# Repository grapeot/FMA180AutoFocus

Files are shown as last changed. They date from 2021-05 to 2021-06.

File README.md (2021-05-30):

## 锐星FMA180自动对焦解决方案

[[English version]](#english)

最近买了一个锐星的FMA180打算拍广域。这个镜子因为口径特别小（40mm f/4.5，焦距180mm），所以没有配一般的对焦器，而是像镜头一样在镜身上有个对焦环。因为用的ZWO EAF默认只支持望远镜对焦器，所以买了传动皮带做了一个自动对焦的装置。分享一下。

其实思路非常简单，就是3D打印一个鸠尾板，然后打印一个装置把EAF用螺丝固定在鸠尾板上。然后用皮带把望远镜（或者其他镜头）的对焦环和EAF连接起来即可。设计出来的模型可以在github下载：https://github.com/grapeot/FMA180AutoFocus/ 。模型如下图：

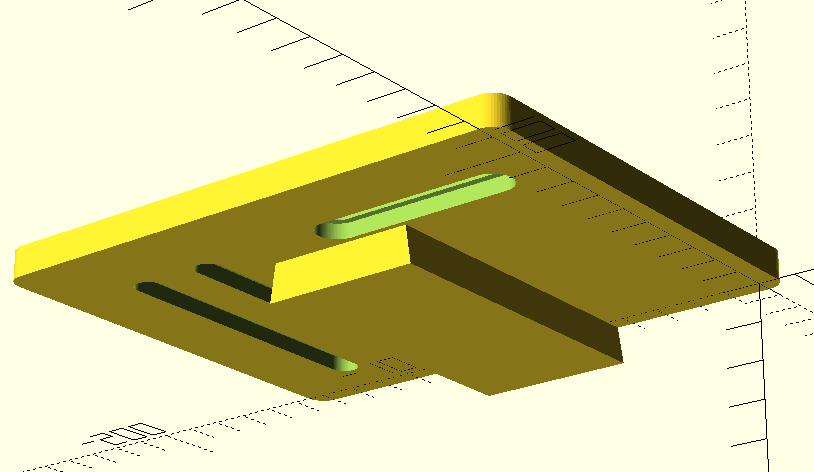
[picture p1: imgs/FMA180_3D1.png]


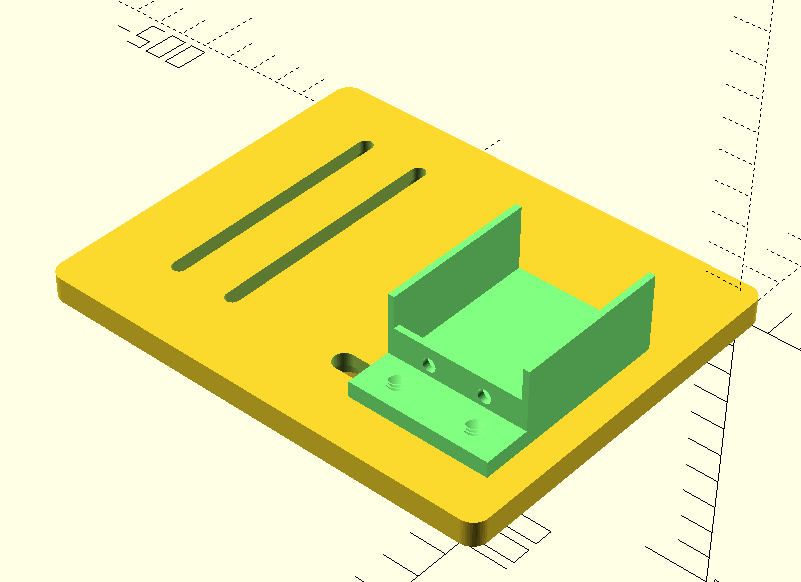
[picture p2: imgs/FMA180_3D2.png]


有几个需要注意的地方：

1. 皮带用的就是GT2皮带，3D打印机上很多也是这种。配套的滑轮（不确定是不是应该叫滑轮？pulley）是5mm的。皮带长度我用的是280mm，这样配套FMA180和鸠尾板的长度正好适配。如果用了其他镜头或者皮带需要重新调整参数。
2. 因为对焦环是凸出来的，所以如果直接安装的话会卡死鸠尾板，导致皮带装不进去。所以我们还需要在上面放四个垫圈。垫圈也是可以打印的，见washer.stl。另外两个STL文件一个是鸠尾板一个是EAF支架。我用的是OpenSCAD开发的，源文件也放进去了。
3. 装配非常简单。基本上把螺丝拧上就好了。固定望远镜用的是随镜附赠的M4螺丝，注意拧的时候要套上垫圈。固定EAF用的是EAF带的M4螺丝（螺距和FMA的M4还不一样）。把EAF支架固定在鸠尾板上用的是M6螺丝，需要另外购买。建议的装配顺序是，先装EAF支架，不要拧死螺丝。然后装FMA主镜，也不要拧死螺丝。然后安装皮带，调整FMA和EAF的位置，左右调EAF，前后调FMA，使得对焦环和EAF平齐，皮带有一定张力。拧紧螺丝。注意EAF支架的螺丝不要太紧，否则可能会破坏打印出来的螺纹。
4. 这个对焦环有个坑是对焦的时候自己会前后跑。所以我的设计是有缺陷的。好在EAF自动对焦的行程不长，只要事先大致拧到合焦的位置（刻度大约是10附近），然后调整FMA的前后位置即可。实测这样是可以可靠自动对焦的。

最终的成品类似这样：

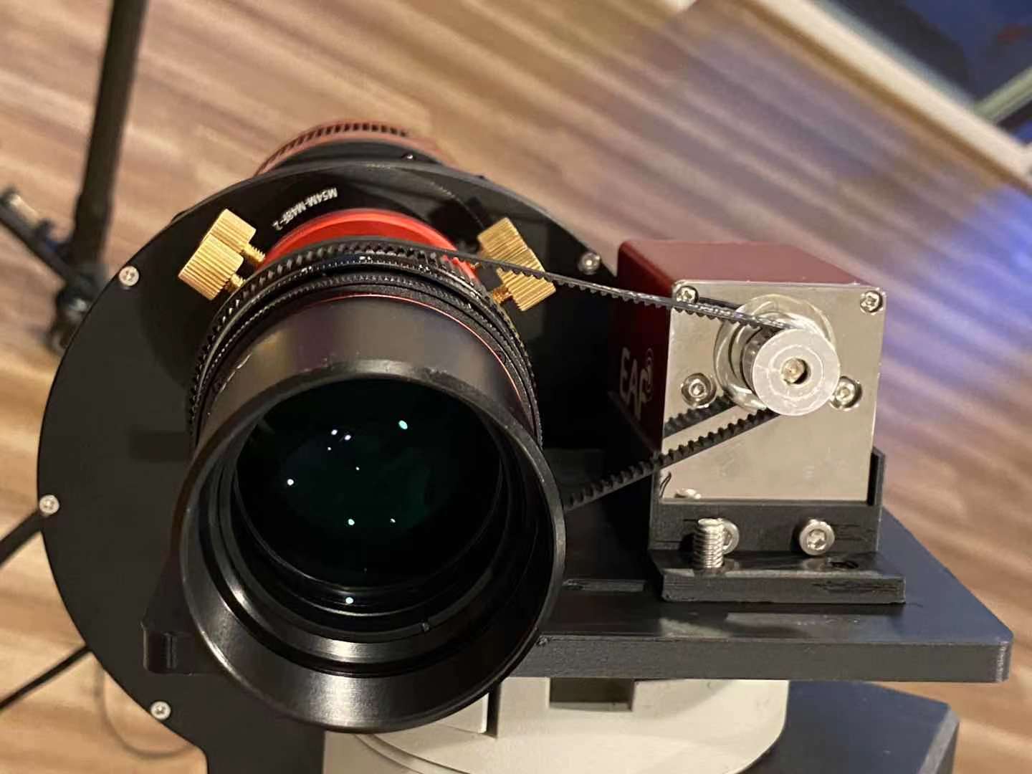
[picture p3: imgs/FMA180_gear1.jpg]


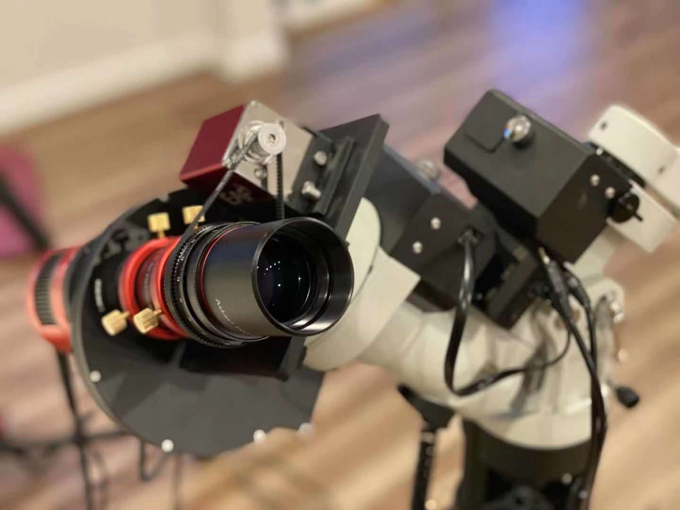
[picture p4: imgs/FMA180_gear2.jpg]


开光拍了个Ha通道2x4的马赛克，总共3小时曝光，效果如图：

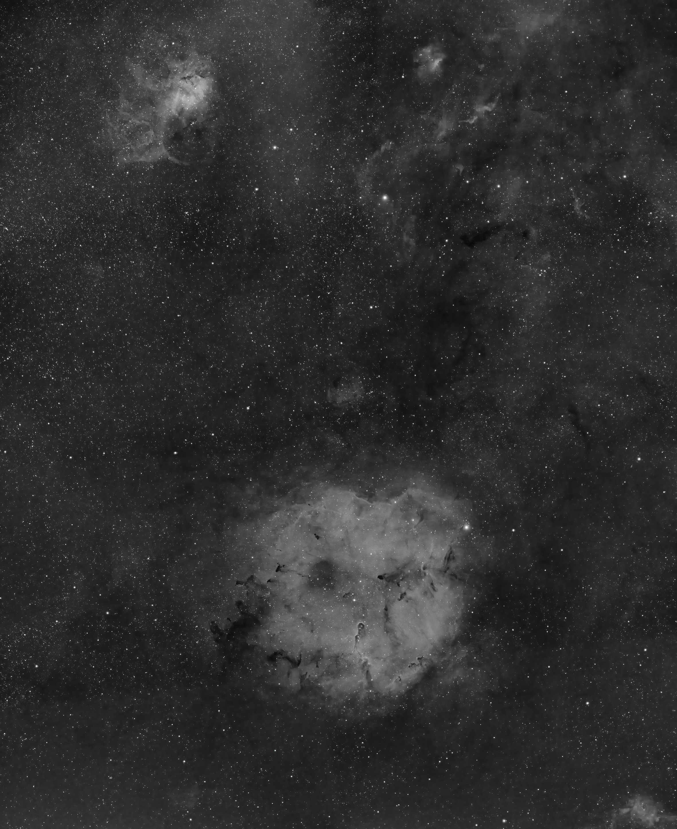
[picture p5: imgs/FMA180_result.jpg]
Result image


## Auto focus solution for SharpStar FMA180

Bought a SharpStar FMA180 recently for wide field use.
Probably because of the small aperture (40mm f/4.5, 180mm focal length), it doesn't come with a regular focuser, but has a focus ring just like regular lens.
But the ZWO EAF I use only supports telescope-style focusers.
So I use a belt to make the EAF work with the FMA180.

The idea is simple.
Just print a dovetail to hold both the scope and a EAF rack, which is then fixed to the dovetail using screws.
The focus ring of the scope (or any lens) can be connected to the EAF via a belt.
The 3d models and instructions can be downloaded on github: https://github.com/grapeot/FMA180AutoFocus/ .
The rendered models look like this:

Rendered model

Rendered model

Several points worth noting:

1. The belt is regular GT2 belt, which can often be found on 3D printers. The The pulley has a bore of 5mm. I use a 280mm length belt, so it fits the FMA180 and the dovetail. When using a belt with a different length or a different scope, you need to adjust the parameters of the dovetail model.
2. Because the focus ring is a bit taller than the scope body, the belt cannot be installed if we directly screw the scope to the dovetail. In this case, four washers are needed between the dovetail and the scope. They are also printable -- check washer.stl. The other two STL files are for the dovetail and the EAF rack. I used OpenSCAD to develop, so I also put the .scad files in the repo.
3. Assembly is easy -- just using screws. To fix the scope to the dovetail, M4 screws with the scope are used. Don't forget to put the washers beforehand. To fix the EAF to the rack, the M4 screws coming with the EAF can be used. Interestingly these two M4 screws have different pitches. To fix the EAF rack to the dovetail, M6 screws are used. Note they need to be bought separately. The suggested assembly order is, first install the EAF rack but leave the screws loose. Then install the FMA scope. Leave the screws loose as well. Then install the belt. Adjust the positions of the FMA and the EAF, such that the EAF pulley and FMA focus ring are aligned, and the belt has enough tension. Then tighten the screws. Pay attention to the screws connecting the EAF rack and the dovetail. Don't over-tighten them. The threads are 3D printed on plastic anyway.
4. One caveat of FMA180 is the focus ring actually moves when focusing. My design doesn't accommodate this. So in order for the auto focus to work properly, before installing the FMA180, you need to roughly focus the scope. I find 10mm on the focus ring gives me good results. In this case, given the auto focus process has pretty limited movement, it can be performed reliably.

The final result looks like this:

Final result

Final result

And here is a result of 3 hours' Ha channel, from a 2x4 mosaic:

Result image

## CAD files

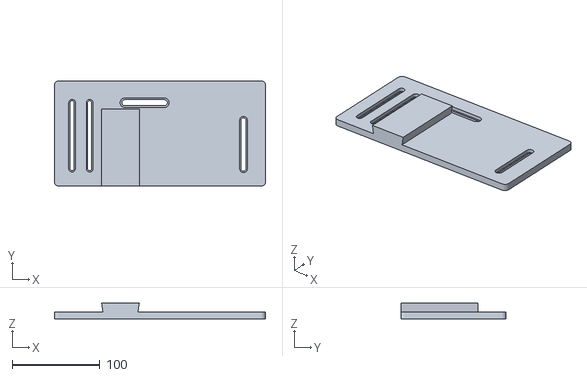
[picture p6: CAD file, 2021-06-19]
dovetail.stl
240.0 x 120.0 x 18.0

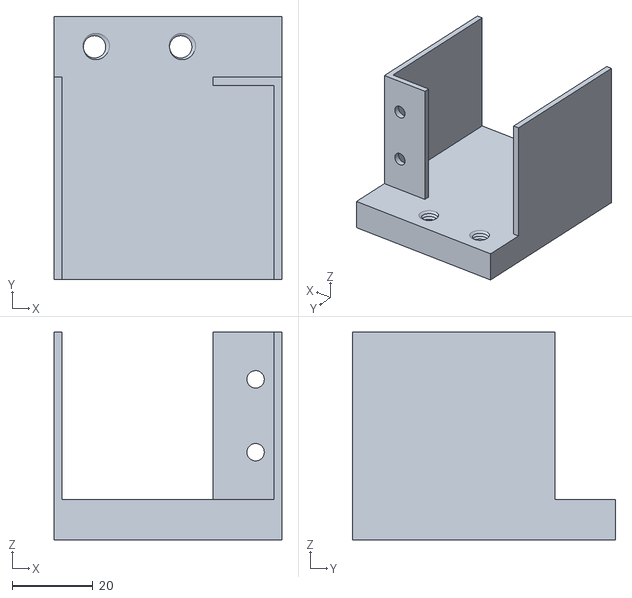
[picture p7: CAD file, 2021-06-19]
EAFRack.stl
56.3 x 65.0 x 51.3

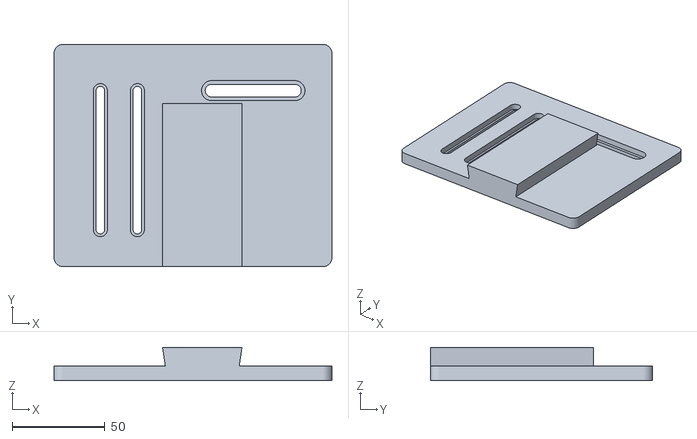
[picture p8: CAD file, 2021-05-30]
dovetail_no_guidescope.stl
150.0 x 120.0 x 18.0

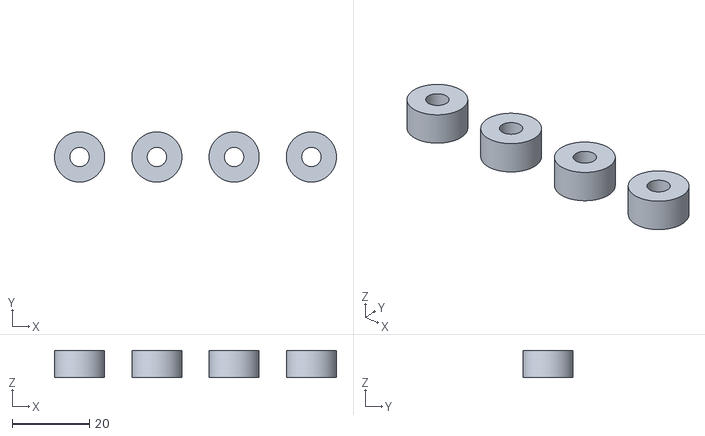
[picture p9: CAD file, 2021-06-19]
washer.stl
73.0 x 13.0 x 7.00

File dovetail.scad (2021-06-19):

include<EAFRack.scad>

module vixen_dovetail(len) {
    height = 10;
    body_height = 0;
    wall_depth = 10;
    margin = 0.6;
    width1 = 43.5 - margin;
    width2 = 40.5 - margin;

    translate([0, -height, 0])
    linear_extrude(height=len)
    polygon(points=[[-width1/2, 0], [-width1/2+wall_depth, 0],
      [-width2/2+wall_depth, height-wall_depth], [width2/2-wall_depth, height-wall_depth],
      [width1/2-wall_depth, 0], [width1/2, 0], 
      [width2/2, height], [-width2/2, height]]);
}

module dovetail_without_guidescope() {
    epsilon = 0.01;

    body_width = 150-10;
    body_height = 110;
    body_left = 15;
    body_top = 90;
    
    screw_upper_depth = 4;

    eaf_margin = 0.4;
    fma_margin = 0.3;

    difference() {
        // body
        linear_extrude(height=8)
        hull() {
            circle(r=5, $fn=50);
            translate([body_width, 0])
            circle(r=5, $fn=50);
            translate([0, body_height])
            circle(r=5, $fn=50);
            translate([body_width, body_height])
            circle(r=5, $fn=50);
        }

        // EAF holes
        // upper
        hull() {
            translate([body_left, body_top, 0])
            cylinder(r=3+eaf_margin, h=20, center=true, $fn=100);
            translate([body_left+45, body_top, 0])
            cylinder(r=3+eaf_margin, h=20, center=true, $fn=100);
        }
        // lower
        hull() {
            translate([body_left, body_top, -epsilon])
            cylinder(r=5+eaf_margin, h=screw_upper_depth, $fn=100);
            translate([body_left+45, body_top, -epsilon])
            cylinder(r=5+eaf_margin, h=screw_upper_depth, $fn=100);
        }

        // FMA holes
        // left
        // upper
        hull() {
            translate([body_left+85, body_top, 0])
            cylinder(r=2+fma_margin, h=20, center=true, $fn=100);
            translate([body_left+85, 15, 0])
            cylinder(r=2+fma_margin, h=20, center=true, $fn=100);
        }
        // lower
        hull() {
            translate([body_left+85, body_top, -epsilon])
            cylinder(r=3.5+fma_margin, h=screw_upper_depth, $fn=100);
            translate([body_left+85, 15, -epsilon])
            cylinder(r=3.5+fma_margin, h=screw_upper_depth, $fn=100);
        }
        // right
        // upper
        hull() {
            translate([body_left+105, body_top, 0])
            cylinder(r=2+fma_margin, h=20, center=true, $fn=100);
            translate([body_left+105, 15, 0])
            cylinder(r=2+fma_margin, h=20, center=true, $fn=100);
        }
        // lower
        hull() {
            translate([body_left+105, body_top, -epsilon])
            cylinder(r=3.5+fma_margin, h=screw_upper_depth, $fn=100);
            translate([body_left+105, 15, -epsilon])
            cylinder(r=3.5+fma_margin, h=screw_upper_depth, $fn=100);
        }
    }

    translate([body_width/2-5, body_height-27, 0])
    rotate([90, 0, 0])
    vixen_dovetail(body_height-22);
}

module dovetail() {
    epsilon = 0.01;

    body_width = 150-10+90;
    body_height = 110;
    body_left = 20;
    body_fma_left = body_left+90;
    body_top = 90;
    
    screw_upper_depth = 4;

    eaf_margin = 0.4;
    fma_margin = 0.3;

    difference() {
        // body
        linear_extrude(height=8)
        hull() {
            circle(r=5, $fn=50);
            translate([body_width, 0])
            circle(r=5, $fn=50);
            translate([0, body_height])
            circle(r=5, $fn=50);
            translate([body_width, body_height])
            circle(r=5, $fn=50);
        }

        // EAF holes
        // upper
        hull() {
            translate([body_fma_left, body_top, 0])
            cylinder(r=3+eaf_margin, h=20, center=true, $fn=100);
            translate([body_fma_left+45, body_top, 0])
            cylinder(r=3+eaf_margin, h=20, center=true, $fn=100);
        }
        // lower
        hull() {
            translate([body_fma_left, body_top, -epsilon])
            cylinder(r=5+eaf_margin, h=screw_upper_depth, $fn=100);
            translate([body_fma_left+45, body_top, -epsilon])
            cylinder(r=5+eaf_margin, h=screw_upper_depth, $fn=100);
        }

        // FMA holes
        // left
        // upper
        hull() {
            translate([body_fma_left+85, body_top, 0])
            cylinder(r=2+fma_margin, h=20, center=true, $fn=100);
            translate([body_fma_left+85, 15, 0])
            cylinder(r=2+fma_margin, h=20, center=true, $fn=100);
        }
        // lower
        hull() {
            translate([body_fma_left+85, body_top, -epsilon])
            cylinder(r=3.5+fma_margin, h=screw_upper_depth, $fn=100);
            translate([body_fma_left+85, 15, -epsilon])
            cylinder(r=3.5+fma_margin, h=screw_upper_depth, $fn=100);
        }
        // right
        // upper
        hull() {
            translate([body_fma_left+105, body_top, 0])
            cylinder(r=2+fma_margin, h=20, center=true, $fn=100);
            translate([body_fma_left+105, 15, 0])
            cylinder(r=2+fma_margin, h=20, center=true, $fn=100);
        }
        // lower
        hull() {
            translate([body_fma_left+105, body_top, -epsilon])
            cylinder(r=3.5+fma_margin, h=screw_upper_depth, $fn=100);
            translate([body_fma_left+105, 15, -epsilon])
            cylinder(r=3.5+fma_margin, h=screw_upper_depth, $fn=100);
        }

        // Guidescope holes
        // upper
        hull() {
            translate([body_left, 70, 0])
            cylinder(r=2.5+eaf_margin, h=20, center=true, $fn=100);
            translate([body_left, 15, 0])
            cylinder(r=2.5+eaf_margin, h=20, center=true, $fn=100);
        }
        // lower
        hull() {
            translate([body_left, 70, -epsilon])
            cylinder(r=4+eaf_margin, h=screw_upper_depth, $fn=100);
            translate([body_left, 15, -epsilon])
            cylinder(r=4+eaf_margin, h=screw_upper_depth, $fn=100);
        }
    }

    translate([body_width/2+45, body_height-27, 0])
    rotate([90, 0, 0])
    vixen_dovetail(body_height-22);
}

module washer() {
    $fn=100;
    linear_extrude(height=3) {
        difference() {
            circle(r=6.5);
            circle(r=2.5);
        }
    }
}

// rotate([0, 180, 0])
// {
//     dovetail();
//     // dovetail_without_guidescope();
//     // color([0.5, 1.0, 0.5])
//     // translate([25, 87, 15])
//     // rotate([90, 0, 0])
//     // eaf_rack();
// }
for (i = [0: 3])
    translate([i*20, 0, 0])
    washer();

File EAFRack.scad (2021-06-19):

include<M6Screw.scad>

module m6_screw_hole() {
    clearance = 0.3;
    diameter = 6;
    length = 20;
    tolerance = 0.4;

    ScrewThread(diameter + 1.4, length+0.01, tolerance=tolerance,
        tip_height=ThreadPitch(diameter), tip_min_fract=0.75);
}

module eaf_rack() {
    $fn=50;

    margin = 0.3;
    rack_wall_depth = 2;
    rack_wall_depth_bottom = 4;
    rack_width = 41 + margin;
    rack_height = 20;
    rack_depth = 50;

    eaf_screw_panel_depth = 2;
    eaf_screw_panel_hole_radius = (4+margin)/2;
    eaf_screw_panel_hole_width = 18;
    eaf_screw_panel_hole_height = 4.5;

    dovetail_hole_panel_depth = 5;
    dovetail_hole_panel_height = 15;
    
    // rack body
    linear_extrude(height=rack_depth)
    polygon(points=[
        [-rack_wall_depth-rack_width/2, -rack_wall_depth_bottom],
        [rack_wall_depth+rack_width/2, -rack_wall_depth_bottom],
        [rack_wall_depth+rack_width/2, rack_height],
        [rack_width/2, rack_height],
        [rack_width/2, 0],
        [-rack_width/2, 0],
        [-rack_width/2, rack_height],
        [-rack_wall_depth-rack_width/2, rack_height]
    ]);
    
    // panel for the EAF screws
    linear_extrude(height=eaf_screw_panel_depth)
    difference() {
        translate([-rack_width/2, 0])
        square(size=[rack_width, rack_height/2]);
        translate([-eaf_screw_panel_hole_width/2, eaf_screw_panel_hole_height])
        circle(r=eaf_screw_panel_hole_radius);
        translate([eaf_screw_panel_hole_width/2, eaf_screw_panel_hole_height])
        circle(r=eaf_screw_panel_hole_radius);
    }

    // screw holes for the dovetail
    translate([-(rack_wall_depth+rack_width/2), -rack_wall_depth_bottom, -dovetail_hole_panel_height])
    difference() {
        cube([rack_wall_depth*2+rack_width, dovetail_hole_panel_depth, dovetail_hole_panel_height]);
        translate([10, 8, dovetail_hole_panel_height/2])
        rotate([90, 0, 0])
        m6_screw_hole();
        translate([rack_wall_depth*2+rack_width-10, 8, dovetail_hole_panel_height/2])
        rotate([90, 0, 0])
        m6_screw_hole();
    }
}

// Put the EAF horizontal so it's aligned with the center of the scope
module eaf_rack_v2() {
    $fn=50;

    margin = 0.3;
    rack_wall_depth = 2;
    rack_wall_depth_bottom = 10;
    rack_width = 41 + margin;
    rack_height = 52 + margin;
    rack_depth = 50;

    eaf_screw_panel_depth = 2;
    eaf_screw_panel_hole_radius = (4+margin)/2;
    eaf_screw_panel_hole_width = 18;
    eaf_screw_panel_hole_height = 4.5;

    dovetail_hole_panel_depth = 10;
    dovetail_hole_panel_height = 15;
    
    // rack body
    linear_extrude(height=rack_depth)
    polygon(points=[
        [-rack_wall_depth-rack_height/2, -rack_wall_depth_bottom],
        [rack_wall_depth+rack_height/2, -rack_wall_depth_bottom],
        [rack_wall_depth+rack_height/2, rack_width],
        [rack_height/2, rack_width],
        [rack_height/2, 0],
        [-rack_height/2, 0],
        [-rack_height/2, rack_width],
        [-rack_wall_depth-rack_height/2, rack_width]
    ]);
    
    // panel for the EAF screws
    translate([rack_height/2, 0, 0]) 
    rotate([0, 0, 90])
    linear_extrude(height=eaf_screw_panel_depth)
    difference() {
        square(size=[rack_width, 15]);
        translate([-eaf_screw_panel_hole_width/2+rack_width/2, eaf_screw_panel_hole_height])
        circle(r=eaf_screw_panel_hole_radius);
        translate([eaf_screw_panel_hole_width/2+rack_width/2, eaf_screw_panel_hole_height])
        circle(r=eaf_screw_panel_hole_radius);
    }

    // screw holes for the dovetail
    translate([-(rack_wall_depth+rack_height/2), -rack_wall_depth_bottom, -dovetail_hole_panel_height])
    difference() {
        cube([rack_wall_depth*2+rack_height, dovetail_hole_panel_depth, dovetail_hole_panel_height]);
        translate([10, 16, dovetail_hole_panel_height/2])
        rotate([90, 0, 0])
        m6_screw_hole();
        translate([rack_wall_depth*2+rack_height-25, 16, dovetail_hole_panel_height/2])
        rotate([90, 0, 0])
        m6_screw_hole();
    }
}

rotate([90, 0, 0])
eaf_rack_v2();

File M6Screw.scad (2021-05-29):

// Created 2016-2017 by Ryan A. Colyer.
// This work is released with CC0 into the public domain.
// https://creativecommons.org/publicdomain/zero/1.0/
//
// http://www.thingiverse.com/thing:1686322
//
// v2.1


screw_resolution = 0.2;  // in mm


// Provides standard metric thread pitches.
function ThreadPitch(diameter) =
  (diameter <= 64) ?
    lookup(diameter, [
      [2, 0.4],
      [2.5, 0.45],
      [3, 0.5],
      [4, 0.7],
      [5, 0.8],
      [6, 1.0],
      [7, 1.0],
      [8, 1.25],
      [10, 1.5],
      [12, 1.75],
      [14, 2.0],
      [16, 2.0],
      [18, 2.5],
      [20, 2.5],
      [22, 2.5],
      [24, 3.0],
      [27, 3.0],
      [30, 3.5],
      [33, 3.5],
      [36, 4.0],
      [39, 4.0],
      [42, 4.5],
      [48, 5.0],
      [52, 5.0],
      [56, 5.5],
      [60, 5.5],
      [64, 6.0]
    ]) :
    diameter * 6.0 / 64;


// Provides standard metric hex head widths across the flats.
function HexAcrossFlats(diameter) =
  (diameter <= 64) ?
    lookup(diameter, [
      [2, 4],
      [2.5, 5],
      [3, 5.5],
      [3.5, 6],
      [4, 7],
      [5, 8],
      [6, 10],
      [7, 11],
      [8, 13],
      [10, 16],
      [12, 18],
      [14, 21],
      [16, 24],
      [18, 27],
      [20, 30],
      [22, 34],
      [24, 36],
      [27, 41],
      [30, 46],
      [33, 50],
      [36, 55],
      [39, 60],
      [42, 65],
      [48, 75],
      [52, 80],
      [56, 85],
      [60, 90],
      [64, 95]
    ]) :
    diameter * 95 / 64;

// Provides standard metric hex head widths across the corners.
function HexAcrossCorners(diameter) =
  HexAcrossFlats(diameter) / cos(30);


// Provides standard metric hex (Allen) drive widths across the flats.
function HexDriveAcrossFlats(diameter) =
  (diameter <= 64) ?
    lookup(diameter, [
      [2, 1.5],
      [2.5, 2],
      [3, 2.5],
      [3.5, 3],
      [4, 3],
      [5, 4],
      [6, 5],
      [7, 5],
      [8, 6],
      [10, 8],
      [12, 10],
      [14, 12],
      [16, 14],
      [18, 15],
      [20, 17],
      [22, 18],
      [24, 19],
      [27, 20],
      [30, 22],
      [33, 24],
      [36, 27],
      [39, 30],
      [42, 32],
      [48, 36],
      [52, 36],
      [56, 41],
      [60, 42],
      [64, 46]
    ]) :
    diameter * 46 / 64;

// Provides standard metric hex (Allen) drive widths across the corners.
function HexDriveAcrossCorners(diameter) =
  HexDriveAcrossFlats(diameter) / cos(30);

// Provides metric countersunk hex (Allen) drive widths across the flats.
function CountersunkDriveAcrossFlats(diameter) =
  (diameter <= 14) ?
    HexDriveAcrossFlats(HexDriveAcrossFlats(diameter)) :
    round(0.6*diameter);

// Provides metric countersunk hex (Allen) drive widths across the corners.
function CountersunkDriveAcrossCorners(diameter) =
  CountersunkDriveAcrossFlats(diameter) / cos(30);

// Provides standard metric nut thickness.
function NutThickness(diameter) =
  (diameter <= 64) ?
    lookup(diameter, [
      [2, 1.6],
      [2.5, 2],
      [3, 2.4],
      [3.5, 2.8],
      [4, 3.2],
      [5, 4.7],
      [6, 5.2],
      [7, 6.0],
      [8, 6.8],
      [10, 8.4],
      [12, 10.8],
      [14, 12.8],
      [16, 14.8],
      [18, 15.8],
      [20, 18.0],
      [22, 21.1],
      [24, 21.5],
      [27, 23.8],
      [30, 25.6],
      [33, 28.7],
      [36, 31.0],
      [42, 34],
      [48, 38],
      [56, 45],
      [64, 51]
    ]) :
    diameter * 51 / 64;
  

// This generates a closed polyhedron from an array of arrays of points,
// with each inner array tracing out one loop outlining the polyhedron.
// pointarrays should contain an array of N arrays each of size P outlining a
// closed manifold.  The points must obey the right-hand rule.  For example,
// looking down, the P points in the inner arrays are counter-clockwise in a
// loop, while the N point arrays increase in height.  Points in each inner
// array do not need to be equal height, but they usually should not meet or
// cross the line segments from the adjacent points in the other arrays.
// (N>=2, P>=3)
// Core triangles:
//   [j][i], [j+1][i], [j+1][(i+1)%P]
//   [j][i], [j+1][(i+1)%P], [j][(i+1)%P]
//   Then triangles are formed in a loop with the middle point of the first
//   and last array.
module ClosePoints(pointarrays) {
  function recurse_avg(arr, n=0, p=[0,0,0]) = (n>=len(arr)) ? p :
    recurse_avg(arr, n+1, p+(arr[n]-p)/(n+1));

  N = len(pointarrays);
  P = len(pointarrays[0]);
  NP = N*P;
  lastarr = pointarrays[N-1];
  midbot = recurse_avg(pointarrays[0]);
  midtop = recurse_avg(pointarrays[N-1]);

  faces_bot = [
    for (i=[0:P-1])
      [0,i+1,1+(i+1)%len(pointarrays[0])]
  ];

  loop_offset = 1;
  bot_len = loop_offset + P;

  faces_loop = [
    for (j=[0:N-2], i=[0:P-1], t=[0:1])
      [loop_offset, loop_offset, loop_offset] + (t==0 ?
      [j*P+i, (j+1)*P+i, (j+1)*P+(i+1)%P] :
      [j*P+i, (j+1)*P+(i+1)%P, j*P+(i+1)%P])
  ];

  top_offset = loop_offset + NP - P;
  midtop_offset = top_offset + P;

  faces_top = [
    for (i=[0:P-1])
      [midtop_offset,top_offset+(i+1)%P,top_offset+i]
  ];

  points = [
    for (i=[-1:NP])
      (i<0) ? midbot :
      ((i==NP) ? midtop :
      pointarrays[floor(i/P)][i%P])
  ];
  faces = concat(faces_bot, faces_loop, faces_top);

  polyhedron(points=points, faces=faces);
}



// This creates a vertical rod at the origin with external threads.  It uses
// metric standards by default.
module ScrewThread(outer_diam, height, pitch=0, tooth_angle=30, tolerance=0.4, tip_height=0, tooth_height=0, tip_min_fract=0) {

  pitch = (pitch==0) ? ThreadPitch(outer_diam) : pitch;
  tooth_height = (tooth_height==0) ? pitch : tooth_height;
  tip_min_fract = (tip_min_fract<0) ? 0 :
    ((tip_min_fract>0.9999) ? 0.9999 : tip_min_fract);

  outer_diam_cor = outer_diam + 0.25*tolerance; // Plastic shrinkage correction
  inner_diam = outer_diam - tooth_height/tan(tooth_angle);
  or = (outer_diam_cor < screw_resolution) ?
    screw_resolution/2 : outer_diam_cor / 2;
  ir = (inner_diam < screw_resolution) ? screw_resolution/2 : inner_diam / 2;
  height = (height < screw_resolution) ? screw_resolution : height;

  steps_per_loop_try = ceil(2*3.14159265359*or / screw_resolution);
  steps_per_loop = (steps_per_loop_try < 4) ? 4 : steps_per_loop_try;
  hs_ext = 3;
  hsteps = ceil(3 * height / pitch) + 2*hs_ext;

  extent = or - ir;

  tip_start = height-tip_height;
  tip_height_sc = tip_height / (1-tip_min_fract);

  tip_height_ir = (tip_height_sc > tooth_height/2) ?
    tip_height_sc - tooth_height/2 : tip_height_sc;

  tip_height_w = (tip_height_sc > tooth_height) ? tooth_height : tip_height_sc;
  tip_wstart = height + tip_height_sc - tip_height - tip_height_w;


  function tooth_width(a, h, pitch, tooth_height, extent) =
    let(
      ang_full = h*360.0/pitch-a,
      ang_pn = atan2(sin(ang_full), cos(ang_full)),
      ang = ang_pn < 0 ? ang_pn+360 : ang_pn,
      frac = ang/360,
      tfrac_half = tooth_height / (2*pitch),
      tfrac_cut = 2*tfrac_half
    )
    (frac > tfrac_cut) ? 0 : (
      (frac <= tfrac_half) ?
        ((frac / tfrac_half) * extent) :
        ((1 - (frac - tfrac_half)/tfrac_half) * extent)
    );


  pointarrays = [
    for (hs=[0:hsteps])
      [
        for (s=[0:steps_per_loop-1])
          let(
            ang_full = s*360.0/steps_per_loop,
            ang_pn = atan2(sin(ang_full), cos(ang_full)),
            ang = ang_pn < 0 ? ang_pn+360 : ang_pn,

            h_fudge = pitch*0.001,

            h_mod =
              (hs%3 == 2) ?
                ((s == steps_per_loop-1) ? tooth_height - h_fudge : (
                 (s == steps_per_loop-2) ? tooth_height/2 : 0)) : (
              (hs%3 == 0) ?
                ((s == steps_per_loop-1) ? pitch-tooth_height/2 : (
                 (s == steps_per_loop-2) ? pitch-tooth_height + h_fudge : 0)) :
                ((s == steps_per_loop-1) ? pitch-tooth_height/2 + h_fudge : (
                 (s == steps_per_loop-2) ? tooth_height/2 : 0))
              ),

            h_level =
              (hs%3 == 2) ? tooth_height - h_fudge : (
              (hs%3 == 0) ? 0 : tooth_height/2),

            h_ub = floor((hs-hs_ext)/3) * pitch
              + h_level + ang*pitch/360.0 - h_mod,
            h_max = height - (hsteps-hs) * h_fudge,
            h_min = hs * h_fudge,
            h = (h_ub < h_min) ? h_min : ((h_ub > h_max) ? h_max : h_ub),
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

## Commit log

2021-05-29 Initial import.
    [EAFRack.scad, M6Screw.scad, dovetail.scad]
2021-05-30 Also include the STL files.
    [EAFRack.stl, dovetail_no_guidescope.stl, washer.stl]
2021-06-07 Add the guidescope slot into the dovetail.
    [dovetail.scad]
2021-06-07 Also add the STL file.
    [dovetail.stl]
2021-06-19 Update the EAF rack design.
    [EAFRack.scad, EAFRack.stl, dovetail.scad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]
